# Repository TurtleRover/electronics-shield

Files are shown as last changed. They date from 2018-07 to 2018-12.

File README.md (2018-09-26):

<p align="center">
  <a href="http://turtlerover.com" alt="Turtle Rover">Turtle Rover</a>
</p>
<h1 align="center">Electronics: Shield</h1>
<h4 align="center">This is Raspberry Pi 3 hat designed for Turtle rover.</h4>  

<p align="center">
  <a href="https://github.com/TurtleRover/electronics-shield/releases">
    </a>
  <a href="https://github.com/TurtleRover/electronics-shield/blob/master/LICENSE">
      
  </a>
  <a href="https://twitter.com/TurtleRover">
    
  </a>
</p>
<p align="center">
  <a href="http://turtlerover.com" alt="Website">Website</a> |
  <a href="https://www.facebook.com/TurtleRover/" alt="Facebook">Facebook</a> |
  <a href="https://www.youtube.com/channel/UCxukvEct3wP0S5FACa3uelA" alt="YouTube">YouTube</a>
</p>

## Specification:

Supply voltage: from 12 V to 28 V  
Equipped with TLE9201SG motor controllers  
Continuous output current per channel: 6 A  
Maximum momentary current per channel: 8 A  
Number of channels: 4  
PWM frequency: up to 20 kHz  
3 x adjustable step-down DC-DC 3A converters   
Built-in STM32F030 microprocessor  
Available interfaces:  
- I2C/UART
- SPI
- USB
- SWD
- 3 x servo

Dedicated to Raspberry Pi B + connectors  
Dimensions: 84 x 56 mm

## Board view
PCB board view

## Connectors standard  

| I2C & Servo  | USB & SPI | Programming  |
| --- | --- | --- |
|   |   |  |

## Manufacturing
Manufacture files are generated and added to release.

### Online view of schematics and layout
View this project on [CADLAB.io](https://cadlab.io/project/1250). 

This git project is intended for using with Eagle PCB.

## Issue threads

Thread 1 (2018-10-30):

Add Real Time Clock module

stsdc, 2018-10-30:

Mictronics, 2018-11-11:
Just a tip:
Route the RTC I2C directly to the Raspberry Pi I2C. In addition, route the DS3231 INT/SQW signal to a Raspberry Pi GPIO. The enable both overlays, i2c-rtc and pps-gpio. This way you have the RTC directly supported by kernel.

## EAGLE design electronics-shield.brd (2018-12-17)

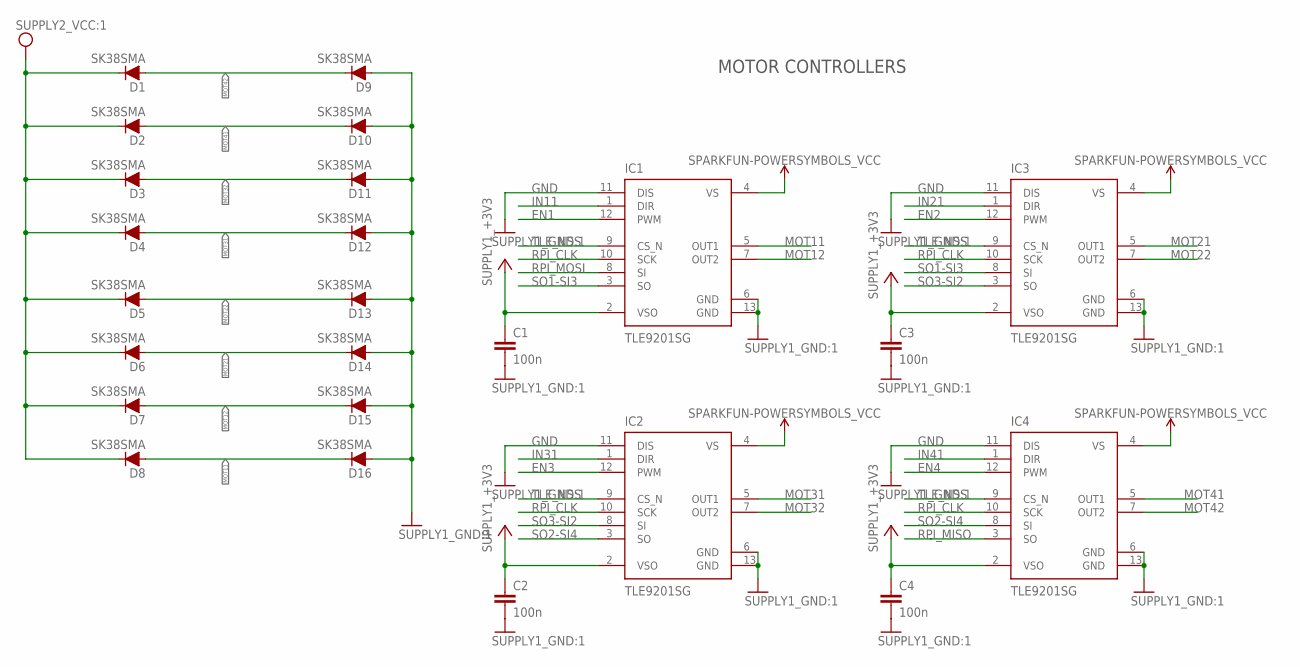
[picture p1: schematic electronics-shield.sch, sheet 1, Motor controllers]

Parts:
C1, C2, C3, C4: 100n; C0603K
D1, D2, D3, D4, D5, D6, D7, D8, D9, D10, D11, D12, D13, D14, D15, D16: SK38SMA; SOD123
IC1, IC2, IC3, IC4: TLE9201SG; PG-DSO-12-9

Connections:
+3V3: C1.1, C2.1, C3.1, C4.1, IC1.2 (VSO), IC2.2 (VSO), IC3.2 (VSO), IC4.2 (VSO); also elsewhere on the board
EN1: IC1.12 (PWM); also elsewhere on the board
EN2: IC3.12 (PWM); also elsewhere on the board
EN3: IC2.12 (PWM); also elsewhere on the board
EN4: IC4.12 (PWM); also elsewhere on the board
GND: C1.2, C2.2, C3.2, C4.2, D9.2 (A), D10.2 (A), D11.2 (A), D12.2 (A), D13.2 (A), D14.2 (A), D15.2 (A), D16.2 (A), IC1.6 (GND), IC1.11 (DIS), IC1.13 (GND), IC2.6 (GND), IC2.11 (DIS), IC2.13 (GND), IC3.6 (GND), IC3.11 (DIS), IC3.13 (GND), IC4.6 (GND), IC4.11 (DIS), IC4.13 (GND); also elsewhere on the board
IN11: IC1.1 (DIR); also elsewhere on the board
IN21: IC3.1 (DIR); also elsewhere on the board
IN31: IC2.1 (DIR); also elsewhere on the board
IN41: IC4.1 (DIR); also elsewhere on the board
MOT11: D8.2 (A), D16.1 (C), IC1.5 (OUT1); also elsewhere on the board
MOT12: D7.2 (A), D15.1 (C), IC1.7 (OUT2); also elsewhere on the board
MOT21: D6.2 (A), D14.1 (C), IC3.5 (OUT1); also elsewhere on the board
MOT22: D5.2 (A), D13.1 (C), IC3.7 (OUT2); also elsewhere on the board
MOT31: D4.2 (A), D12.1 (C), IC2.5 (OUT1); also elsewhere on the board
MOT32: D3.2 (A), D11.1 (C), IC2.7 (OUT2); also elsewhere on the board
MOT41: D2.2 (A), D10.1 (C), IC4.5 (OUT1); also elsewhere on the board
MOT42: D1.2 (A), D9.1 (C), IC4.7 (OUT2); also elsewhere on the board
RPI_CLK: IC1.10 (SCK), IC2.10 (SCK), IC3.10 (SCK), IC4.10 (SCK); also elsewhere on the board
RPI_MISO: IC4.3 (SO); also elsewhere on the board
RPI_MOSI: IC1.8 (SI); also elsewhere on the board
SO1-SI3: IC1.3 (SO), IC3.8 (SI)
SO2-SI4: IC2.3 (SO), IC4.8 (SI)
SO3-SI2: IC2.8 (SI), IC3.3 (SO)
TLE_NSS: IC1.9 (CS_N), IC2.9 (CS_N), IC3.9 (CS_N), IC4.9 (CS_N); also elsewhere on the board
VCC: D1.1 (C), D2.1 (C), D3.1 (C), D4.1 (C), D5.1 (C), D6.1 (C), D7.1 (C), D8.1 (C), IC1.4 (VS), IC2.4 (VS), IC3.4 (VS), IC4.4 (VS); also elsewhere on the board

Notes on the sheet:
MOTOR CONTROLLERS

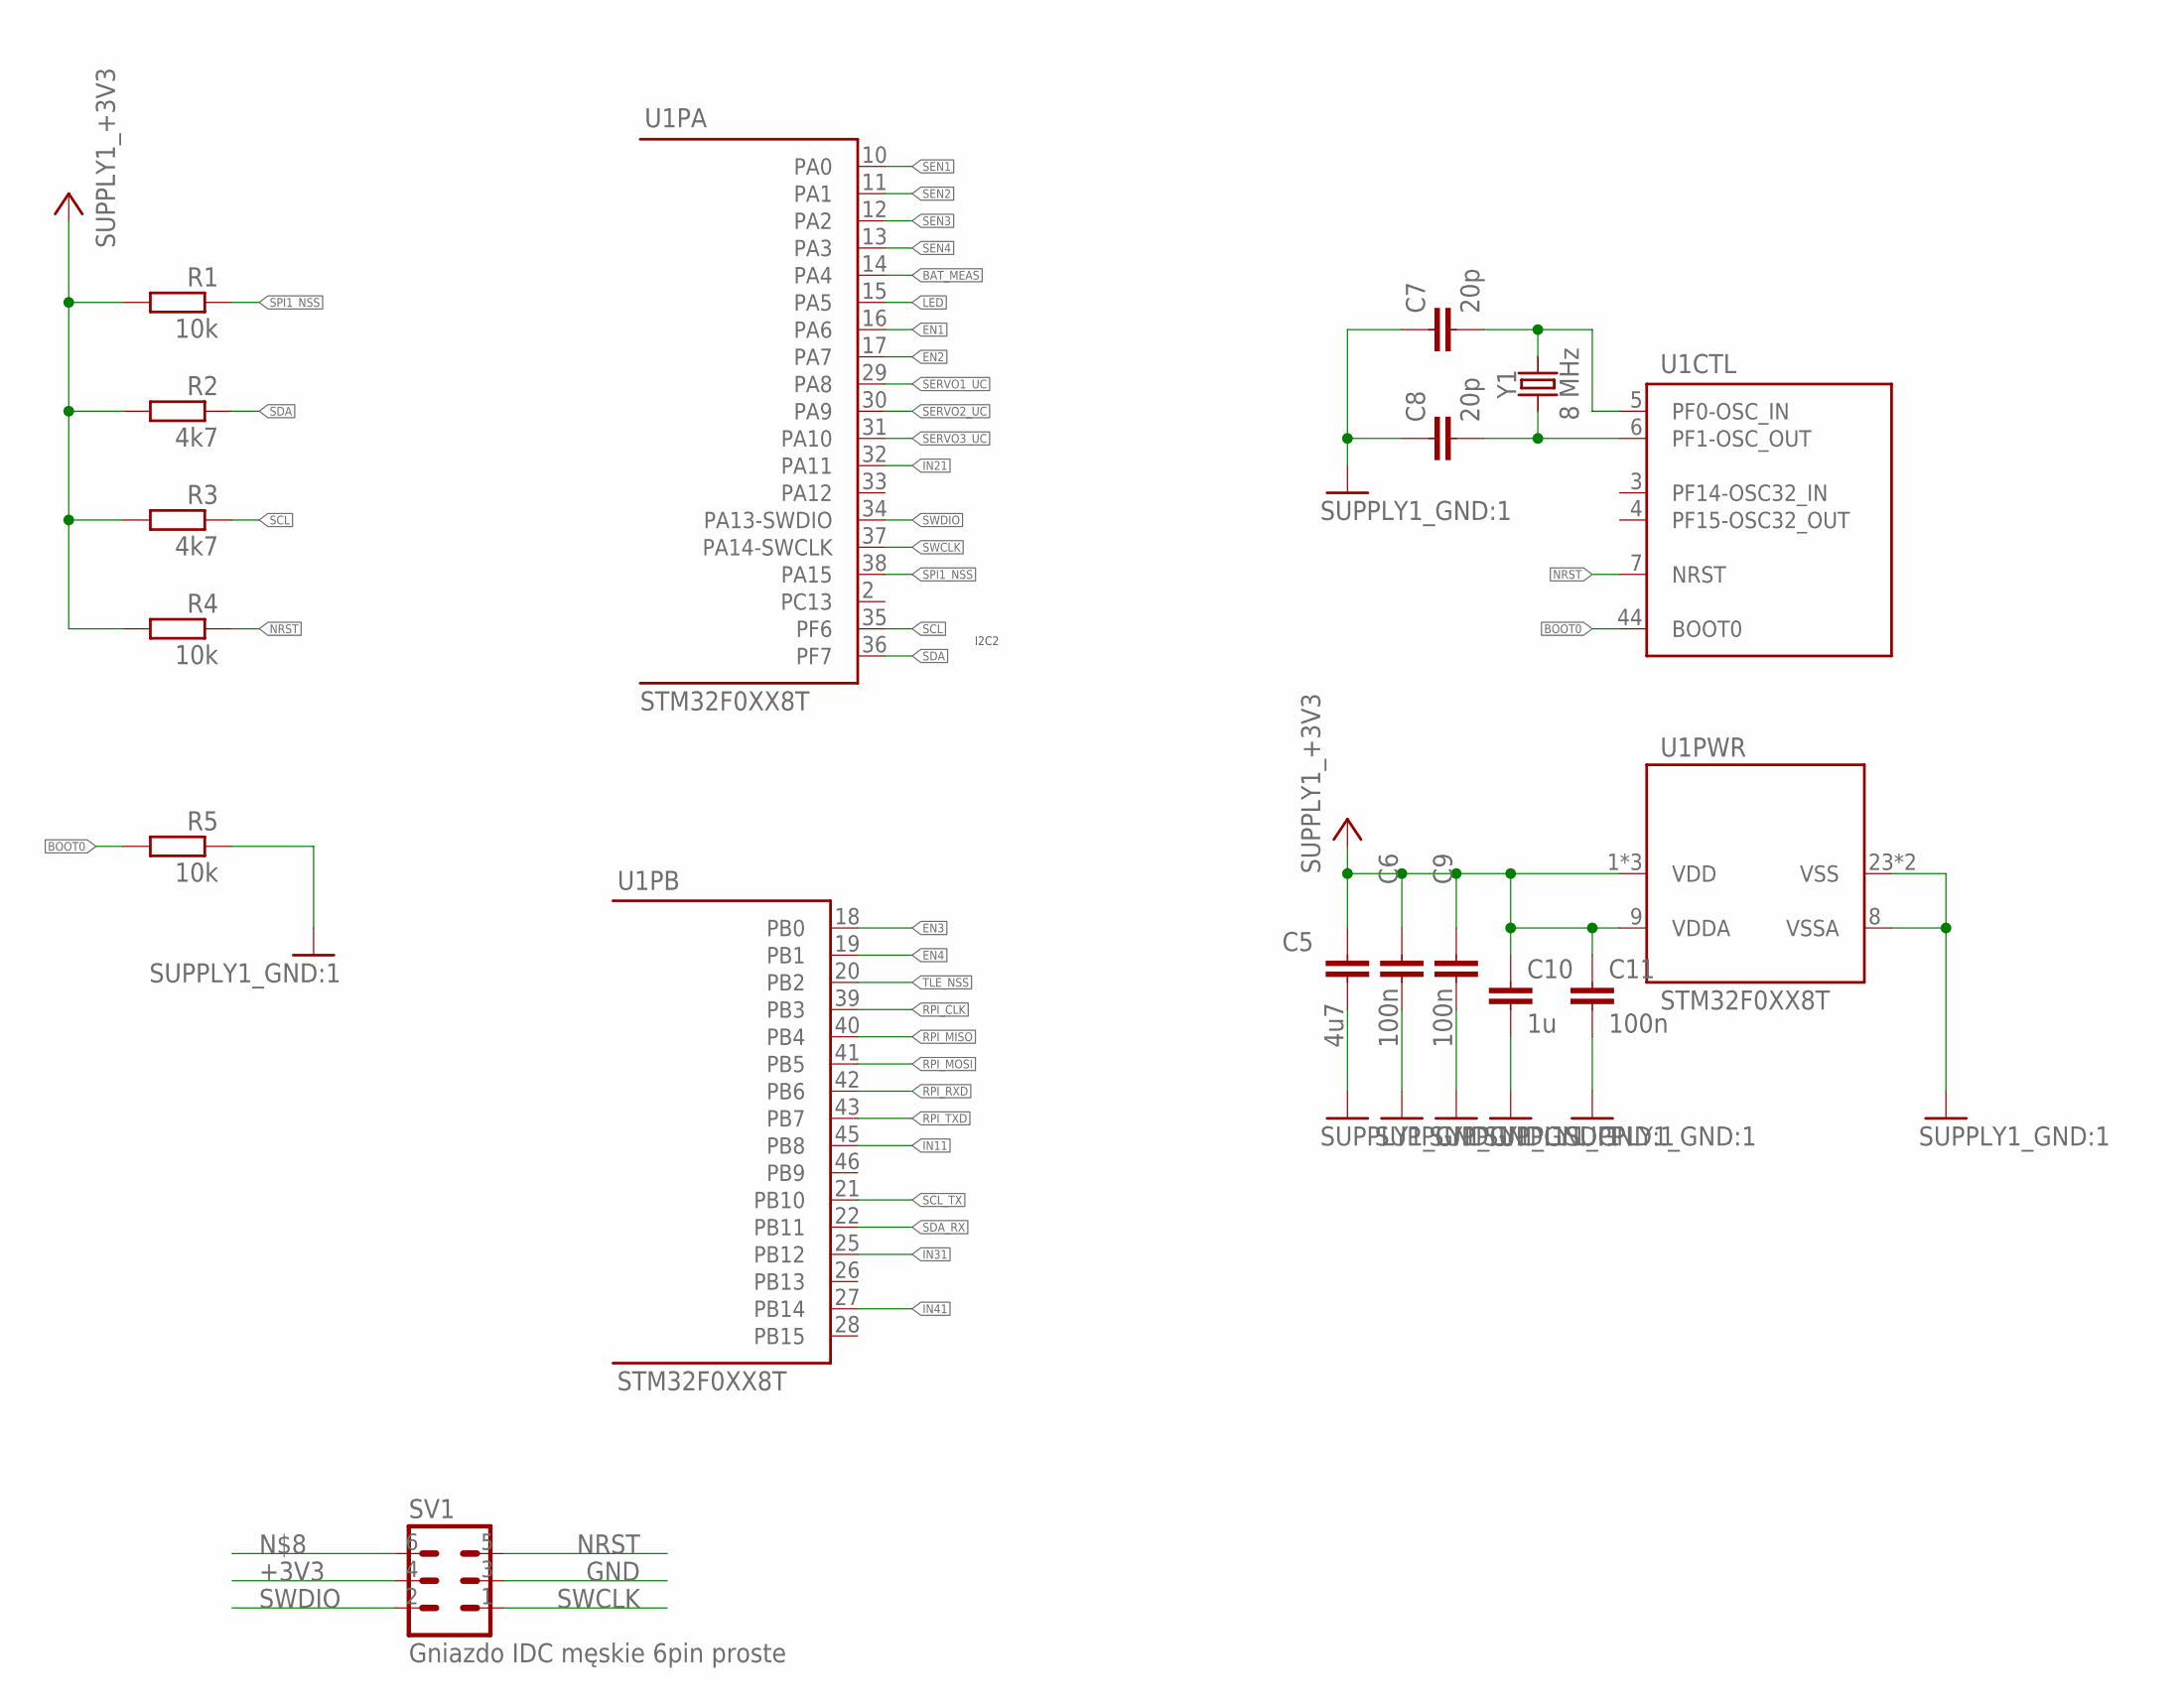
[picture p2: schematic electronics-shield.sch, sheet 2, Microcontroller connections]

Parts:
C5: 4u7; C0603K
C6, C9, C11: 100n; C0603K
C7, C8: 20p; C0603K
C10: 1u; C0603K
R1, R4, R5: 10k; R0603
R2, R3: 4k7; R0603
SV1: Gniazdo IDC męskie 6pin proste; ML6
U1: STM32F0XX8T; LQFP48
Y1: 8 MHz; HC49UP

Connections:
+3V3: C5.1, C6.1, C9.1, C10.1, C11.1, R1.2, R2.2, R3.2, R4.2, SV1.4, U1.1 (VDD), U1.9 (VDDA), U1.24 (VDD), U1.48 (VDD); also elsewhere on the board
BAT_MEAS: U1.14 (PA4); also elsewhere on the board
BOOT0: R5.2, U1.44 (BOOT0)
EN1: U1.16 (PA6); also elsewhere on the board
EN2: U1.17 (PA7); also elsewhere on the board
EN3: U1.18 (PB0); also elsewhere on the board
EN4: U1.19 (PB1); also elsewhere on the board
GND: C5.2, C6.2, C7.1, C8.1, C9.2, C10.2, C11.2, R5.1, SV1.3, U1.8 (VSSA), U1.23 (VSS), U1.47 (VSS); also elsewhere on the board
IN11: U1.45 (PB8); also elsewhere on the board
IN21: U1.32 (PA11); also elsewhere on the board
IN31: U1.25 (PB12); also elsewhere on the board
IN41: U1.27 (PB14); also elsewhere on the board
LED: U1.15 (PA5)
NRST: R4.1, SV1.5, U1.7 (NRST); also elsewhere on the board
OSCILATOR_N: C7.2, U1.5 (PF0-OSC_IN), Y1.2
OSCILATOR_P: C8.2, U1.6 (PF1-OSC_OUT), Y1.1
RPI_CLK: U1.39 (PB3); also elsewhere on the board
RPI_MISO: U1.40 (PB4); also elsewhere on the board
RPI_MOSI: U1.41 (PB5); also elsewhere on the board
RPI_RXD: U1.42 (PB6); also elsewhere on the board
RPI_TXD: U1.43 (PB7); also elsewhere on the board
SCL: R3.1, U1.35 (PF6); also elsewhere on the board
SCL_TX: U1.21 (PB10); also elsewhere on the board
SDA: R2.1, U1.36 (PF7); also elsewhere on the board
SDA_RX: U1.22 (PB11); also elsewhere on the board
SEN1: U1.10 (PA0)
SEN2: U1.11 (PA1)
SEN3: U1.12 (PA2)
SEN4: U1.13 (PA3)
SERVO1_UC: U1.29 (PA8); also elsewhere on the board
SERVO2_UC: U1.30 (PA9); also elsewhere on the board
SERVO3_UC: U1.31 (PA10); also elsewhere on the board
SPI1_NSS: R1.1, U1.38 (PA15); also elsewhere on the board
SWCLK: SV1.1, U1.37 (PA14-SWCLK); also elsewhere on the board
SWDIO: SV1.2, U1.34 (PA13-SWDIO); also elsewhere on the board
TLE_NSS: U1.20 (PB2); also elsewhere on the board

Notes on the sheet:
I2C2

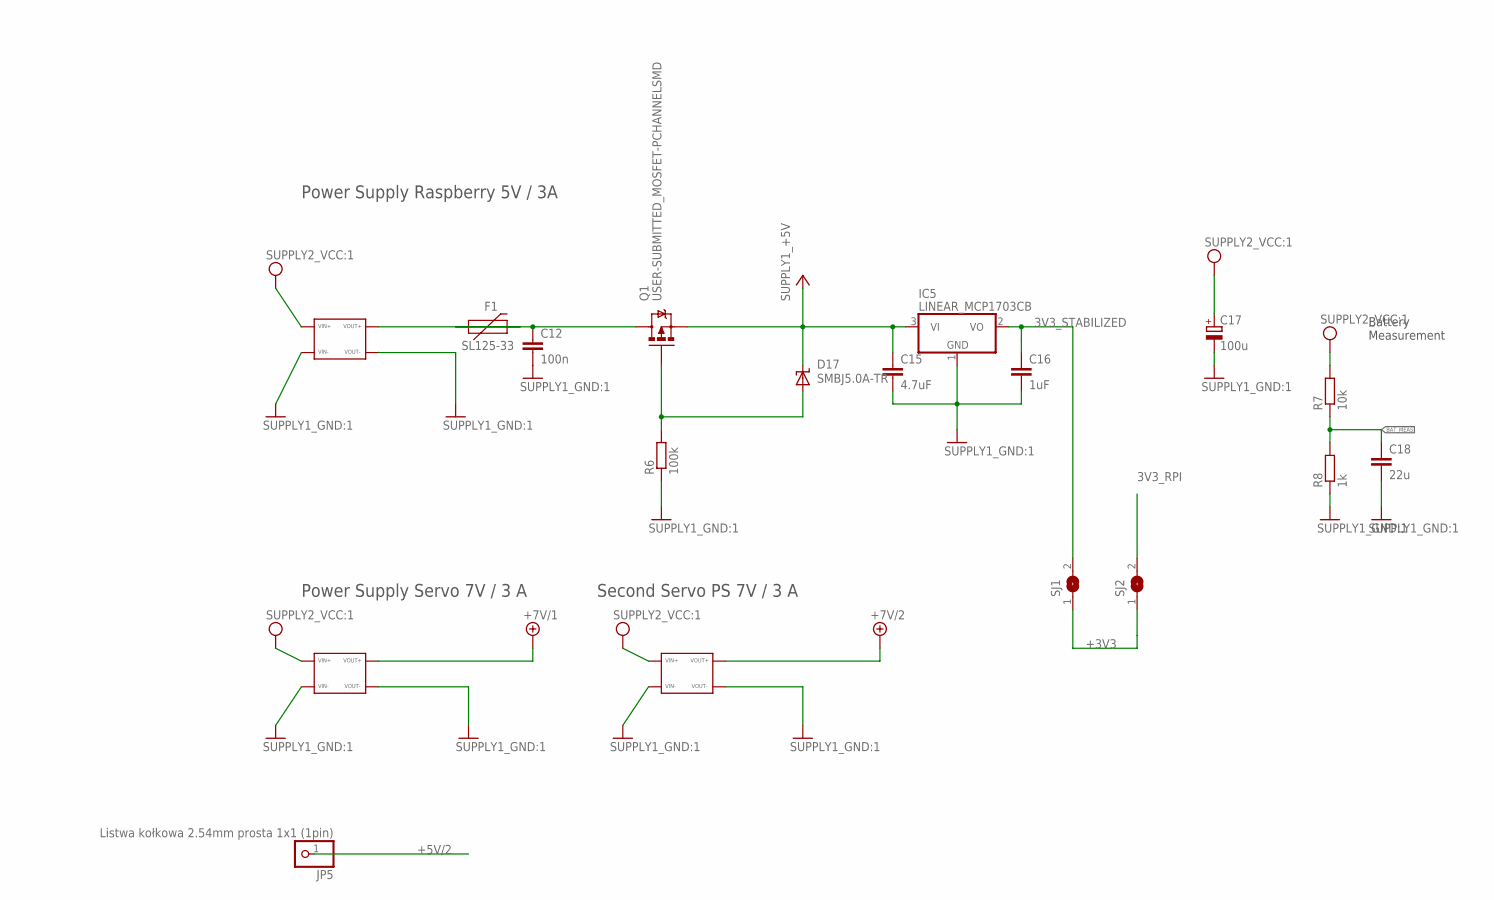
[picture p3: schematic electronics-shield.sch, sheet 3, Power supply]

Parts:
C12: 100n; C0603K
C15: 4.7uF; C0603K
C16: 1uF; C0603K
C17: 100u; FI8_6.2
C18: 22u; C0603K
D17: SMBJ5.0A-TR; SMBJ
F1: SL125-33; FUSC7351X125
IC5: LINEAR_MCP1703CB; LINEAR_SOT23
IC6, IC7, IC8: Moduł przetwornicy DC-DC Step-down 4.5..28V --- r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; DC-BRICK
JP5: Listwa kołkowa 2.54mm prosta 1x1 (1pin); 1X01
Q1: USER-SUBMITTED_MOSFET-PCHANNELSMD; USER-SUBMITTED_SOT23-3
R6: 100k; R0603
R7: 10k; R0603
R8: 1k; R0603
SJ1, SJ2: SOLDER_JUMPER; SJ

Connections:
3V3_RPI: SJ2.2; also elsewhere on the board
3V3_STABILIZED: C16.1, IC5.2 (VO), SJ1.2
5V_NOT_TRIMMED: C12.1, F1.1, Q1.3 (D)
+3V3: SJ1.1, SJ2.1; also elsewhere on the board
+5V: C15.1, D17.C, IC5.3 (VI), Q1.2 (S); also elsewhere on the board
+5V/2: JP5.1; also elsewhere on the board
+5V_RAW: F1.2, IC6.OUT1+1 (VOUT+)
+7V/1: IC7.OUT1+1 (VOUT+); also elsewhere on the board
+7V/2: IC8.OUT1+1 (VOUT+); also elsewhere on the board
BAT_MEAS: C18.1, R7.1, R8.2; also elsewhere on the board
D1-R3: D17.A, Q1.1 (G), R6.2
GND: C12.2, C15.2, C16.2, C17.-, C18.2, IC5.1 (GND), IC6.IN1-1 (VIN-), IC6.OUT1-1 (VOUT-), IC7.IN1-1 (VIN-), IC7.OUT1-1 (VOUT-), IC8.IN1-1 (VIN-), IC8.OUT1-1 (VOUT-), R6.1, R8.1; also elsewhere on the board
VCC: C17.+, IC6.IN1+1 (VIN+), IC7.IN1+1 (VIN+), IC8.IN1+1 (VIN+), R7.2; also elsewhere on the board

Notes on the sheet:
Power Supply Raspberry 5V / 3A
Power Supply Servo 7V / 3 A
Second Servo PS 7V / 3 A
Battery Measurement

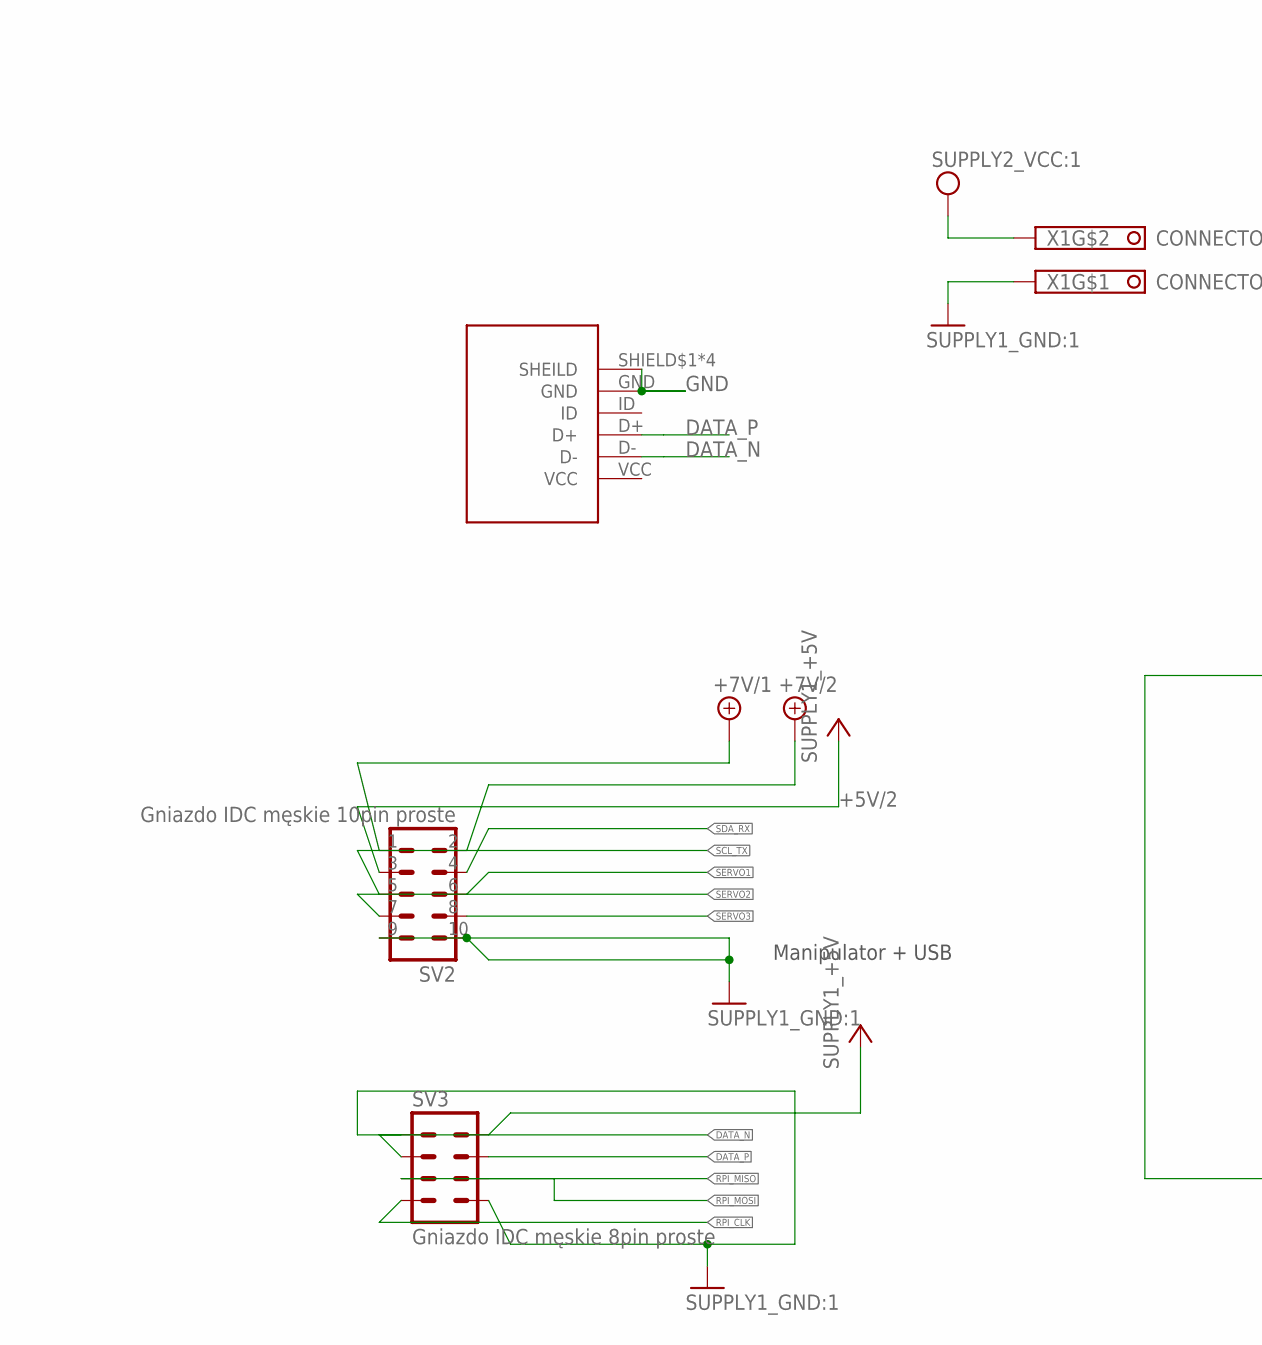
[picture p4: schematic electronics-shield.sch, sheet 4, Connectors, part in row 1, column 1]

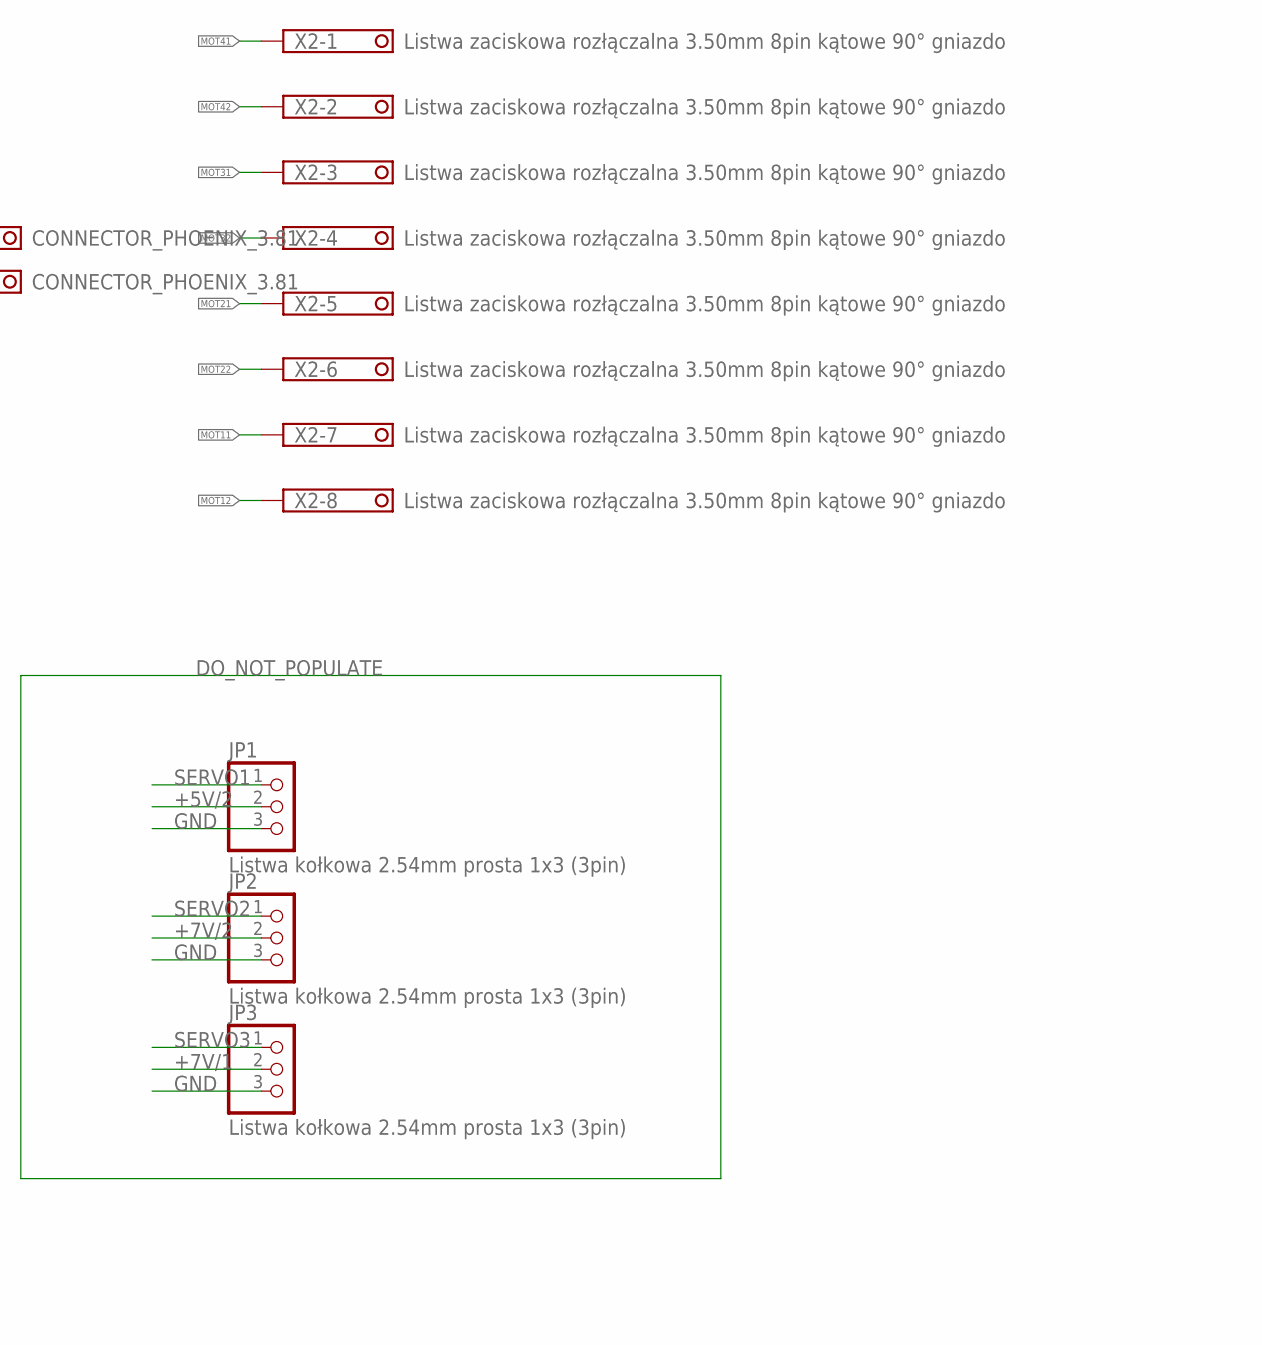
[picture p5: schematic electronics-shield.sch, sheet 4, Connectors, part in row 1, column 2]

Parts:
J1: USB-MICRO-B
JP1, JP2, JP3: Listwa kołkowa 2.54mm prosta 1x3 (3pin); 1X03_ROUND_DNP
SV2: Gniazdo IDC męskie 10pin proste; ML10
SV3: Gniazdo IDC męskie 8pin proste; ML8
X1: CONNECTOR_PHOENIX_3.81; 3.81MM_2PIN
X2: Listwa zaciskowa rozłączalna 3.50mm 8pin kątowe 9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; 3.5MM_8PIN

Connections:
+5V: SV3.2; also elsewhere on the board
+5V/2: JP1.2, SV2.3; also elsewhere on the board
+7V/1: JP3.2, SV2.1; also elsewhere on the board
+7V/2: JP2.2, SV2.2; also elsewhere on the board
DATA_N: J1.D-, SV3.3
DATA_P: J1.D+, SV3.4
GND: J1.GND, J1.SHIELD$1 (SHEILD), J1.SHIELD$2 (SHEILD), J1.SHIELD$3 (SHEILD), J1.SHIELD$4 (SHEILD), JP1.3, JP2.3, JP3.3, SV2.9, SV2.10, SV3.1, SV3.8, X1.1; also elsewhere on the board
MOT11: X2.7; also elsewhere on the board
MOT12: X2.8; also elsewhere on the board
MOT21: X2.5; also elsewhere on the board
MOT22: X2.6; also elsewhere on the board
MOT31: X2.3; also elsewhere on the board
MOT32: X2.4; also elsewhere on the board
MOT41: X2.1; also elsewhere on the board
MOT42: X2.2; also elsewhere on the board
RPI_CLK: SV3.7; also elsewhere on the board
RPI_MISO: SV3.5; also elsewhere on the board
RPI_MOSI: SV3.6; also elsewhere on the board
SCL_TX: SV2.5; also elsewhere on the board
SDA_RX: SV2.4; also elsewhere on the board
SERVO1: JP1.1, SV2.6; also elsewhere on the board
SERVO2: JP2.1, SV2.7; also elsewhere on the board
SERVO3: JP3.1, SV2.8; also elsewhere on the board
VCC: X1.2; also elsewhere on the board

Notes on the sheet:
Manipulator + USB

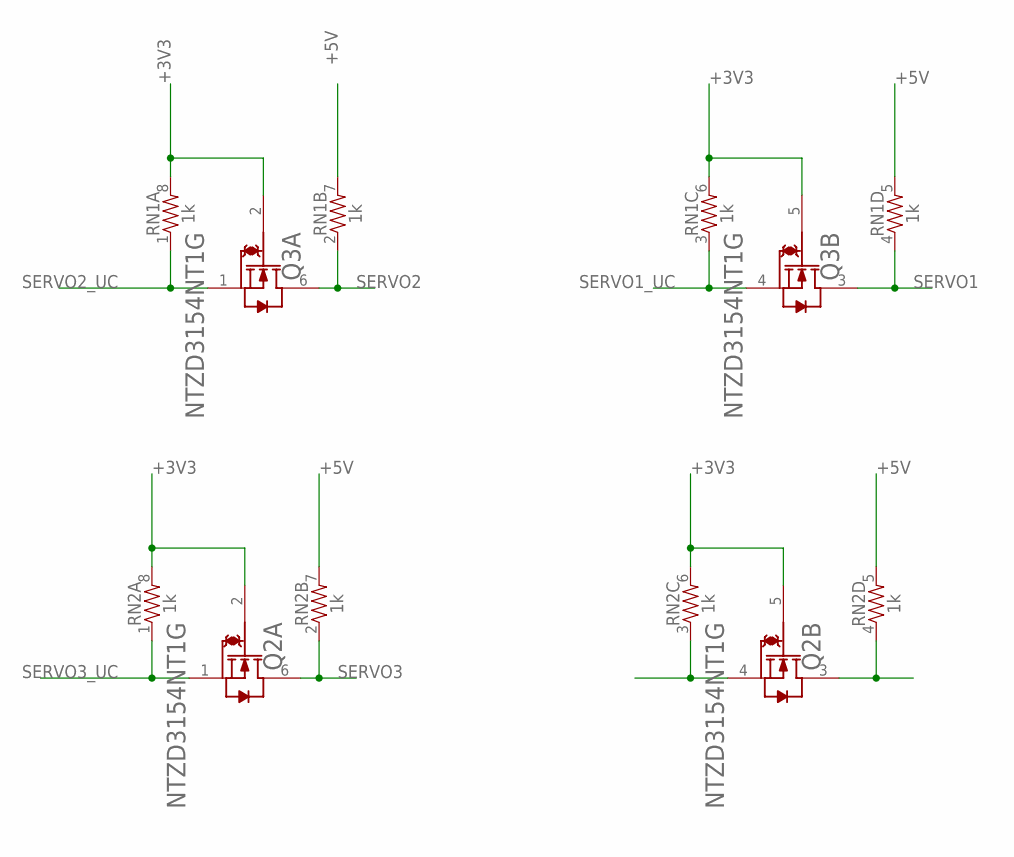
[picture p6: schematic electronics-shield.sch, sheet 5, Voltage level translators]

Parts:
Q2, Q3: NTZD3154NT1G; ON-SEMICONDUCTOR---NTZD3154NT1G_ON_SEMICONDUCTOR_NTZD3154NT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
RN1, RN2: 1k; 0805-ARV

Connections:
+3V3: Q2.2 (G1), Q2.5 (G2), Q3.2 (G1), Q3.5 (G2), RN1.6 (2), RN1.8 (2), RN2.6 (2), RN2.8 (2); also elsewhere on the board
+5V: RN1.5 (2), RN1.7 (2), RN2.5 (2), RN2.7 (2); also elsewhere on the board
unnamed: Q2.4 (S2), RN2.3 (1)
unnamed: Q2.3 (D2), RN2.4 (1)
SERVO1: Q3.3 (D2), RN1.4 (1); also elsewhere on the board
SERVO1_UC: Q3.4 (S2), RN1.3 (1); also elsewhere on the board
SERVO2: Q3.6 (D1), RN1.2 (1); also elsewhere on the board
SERVO2_UC: Q3.1 (S1), RN1.1; also elsewhere on the board
SERVO3: Q2.6 (D1), RN2.2 (1); also elsewhere on the board
SERVO3_UC: Q2.1 (S1), RN2.1; also elsewhere on the board

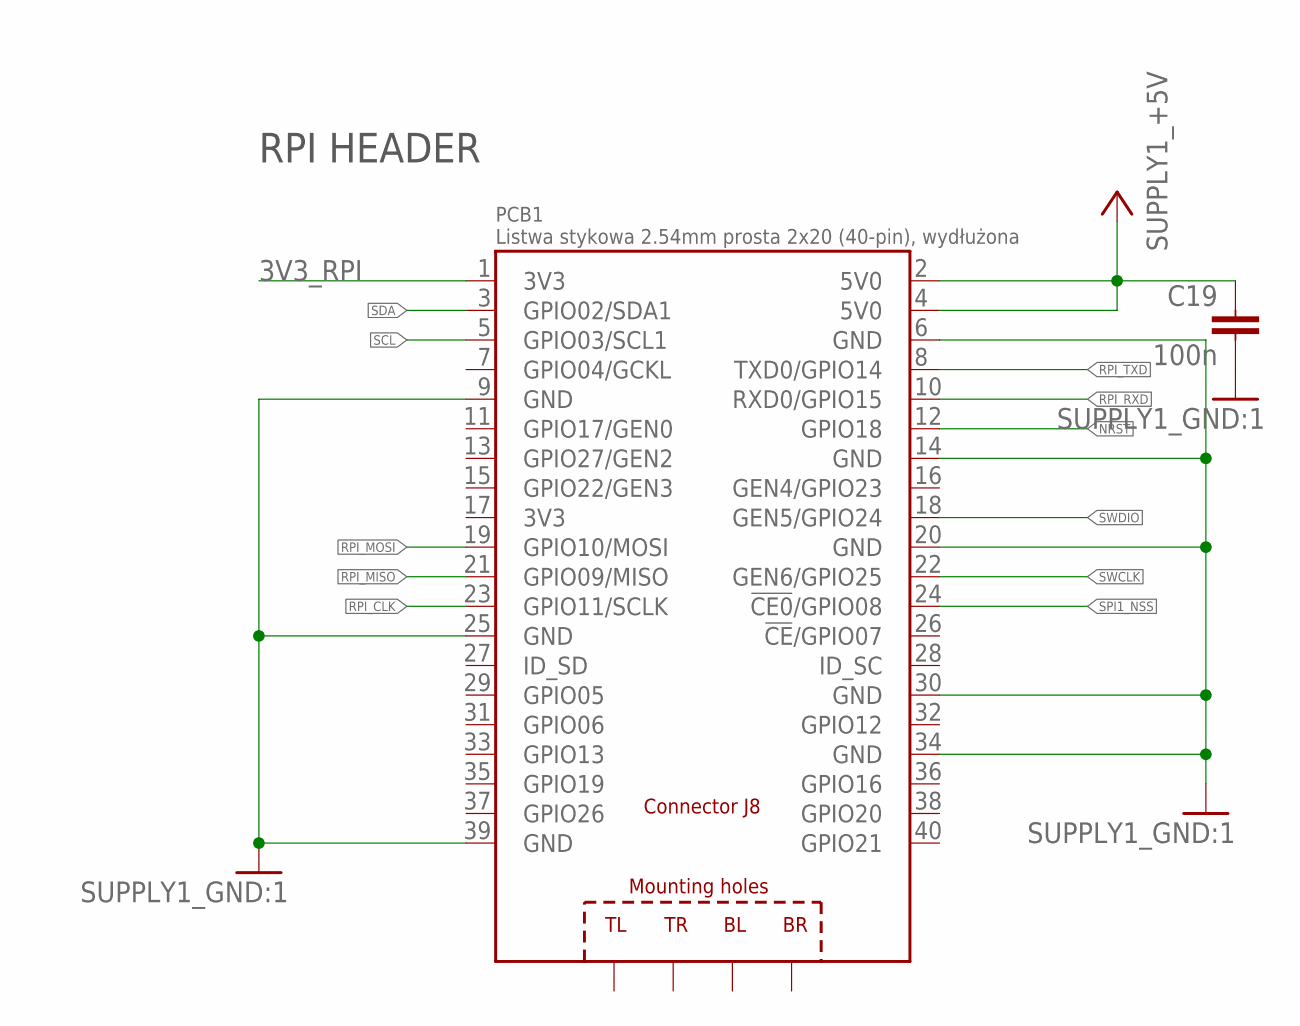
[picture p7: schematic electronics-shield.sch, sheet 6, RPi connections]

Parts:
C19: 100n; C0603K
PCB1: Listwa stykowa 2.54mm prosta 2x20 (40-pin), wydłu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; RASPBERRY_PI_B+_CONNECTOR

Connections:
3V3: PCB1.17 (3V3)
3V3_RPI: PCB1.1 (3V3); also elsewhere on the board
+5V: C19.1, PCB1.2 (5V0), PCB1.4 (5V0); also elsewhere on the board
GND: C19.2, PCB1.6 (GND), PCB1.9 (GND), PCB1.14 (GND), PCB1.20 (GND), PCB1.25 (GND), PCB1.30 (GND), PCB1.34 (GND), PCB1.39 (GND); also elsewhere on the board
NRST: PCB1.12 (GPIO18); also elsewhere on the board
RPI_CLK: PCB1.23 (GPIO11/SCLK); also elsewhere on the board
RPI_MISO: PCB1.21 (GPIO09/MISO); also elsewhere on the board
RPI_MOSI: PCB1.19 (GPIO10/MOSI); also elsewhere on the board
RPI_RXD: PCB1.10 (RXD0/GPIO15); also elsewhere on the board
RPI_TXD: PCB1.8 (TXD0/GPIO14); also elsewhere on the board
SCL: PCB1.5 (GPIO03/SCL1); also elsewhere on the board
SDA: PCB1.3 (GPIO02/SDA1); also elsewhere on the board
SPI1_NSS: PCB1.24 (!CE0!/GPIO08); also elsewhere on the board
SWCLK: PCB1.22 (GEN6/GPIO25); also elsewhere on the board
SWDIO: PCB1.18 (GEN5/GPIO24); also elsewhere on the board

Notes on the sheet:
RPI HEADER

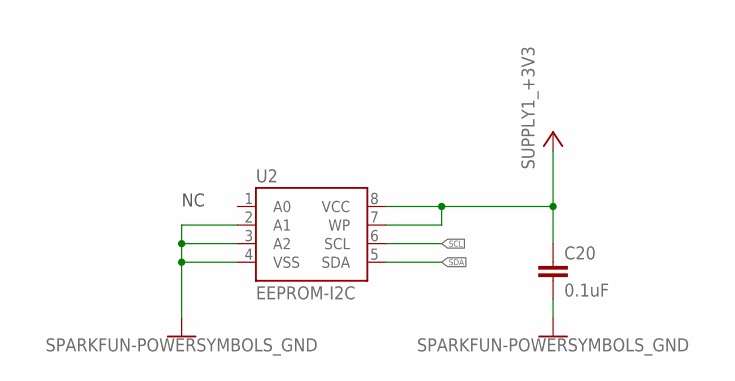
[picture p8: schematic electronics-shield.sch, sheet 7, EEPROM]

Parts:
C20: 0.1uF; C0603K
U2: EEPROM-I2C; SO-08

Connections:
+3V3: C20.1, U2.7 (WP), U2.8 (VCC); also elsewhere on the board
GND: C20.2, U2.2 (A1), U2.3 (A2), U2.4 (VSS); also elsewhere on the board
SCL: U2.6 (SCL); also elsewhere on the board
SDA: U2.5 (SDA); also elsewhere on the board

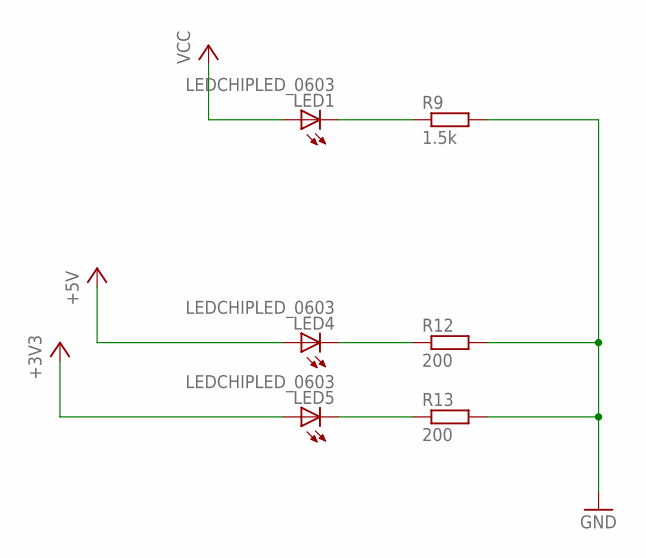
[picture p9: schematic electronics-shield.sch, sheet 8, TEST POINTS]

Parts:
LED1, LED4, LED5: LEDCHIPLED_0603; CHIPLED_0603
R9: 1.5k; R0603
R12, R13: 200; R0603

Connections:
+3V3: LED5.A; also elsewhere on the board
+5V: LED4.A; also elsewhere on the board
GND: R9.2, R12.2, R13.2; also elsewhere on the board
unnamed: LED1.C, R9.1
unnamed: LED4.C, R12.1
unnamed: LED5.C, R13.1
VCC: LED1.A; also elsewhere on the board

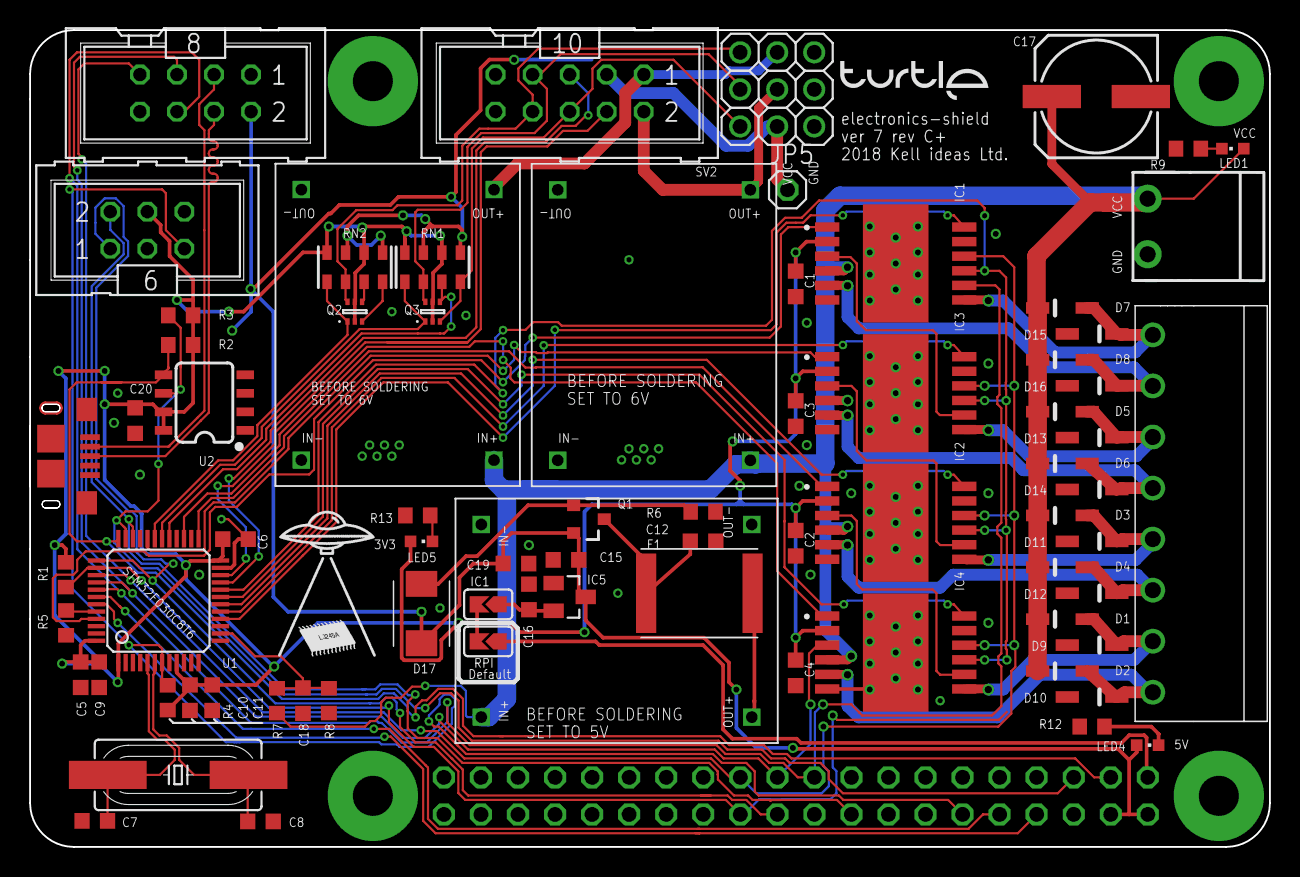
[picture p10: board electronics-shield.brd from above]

Board: 2 copper layers, 85.0 x 56.0 mm, 79 parts (0 on the bottom side), 62 nets.

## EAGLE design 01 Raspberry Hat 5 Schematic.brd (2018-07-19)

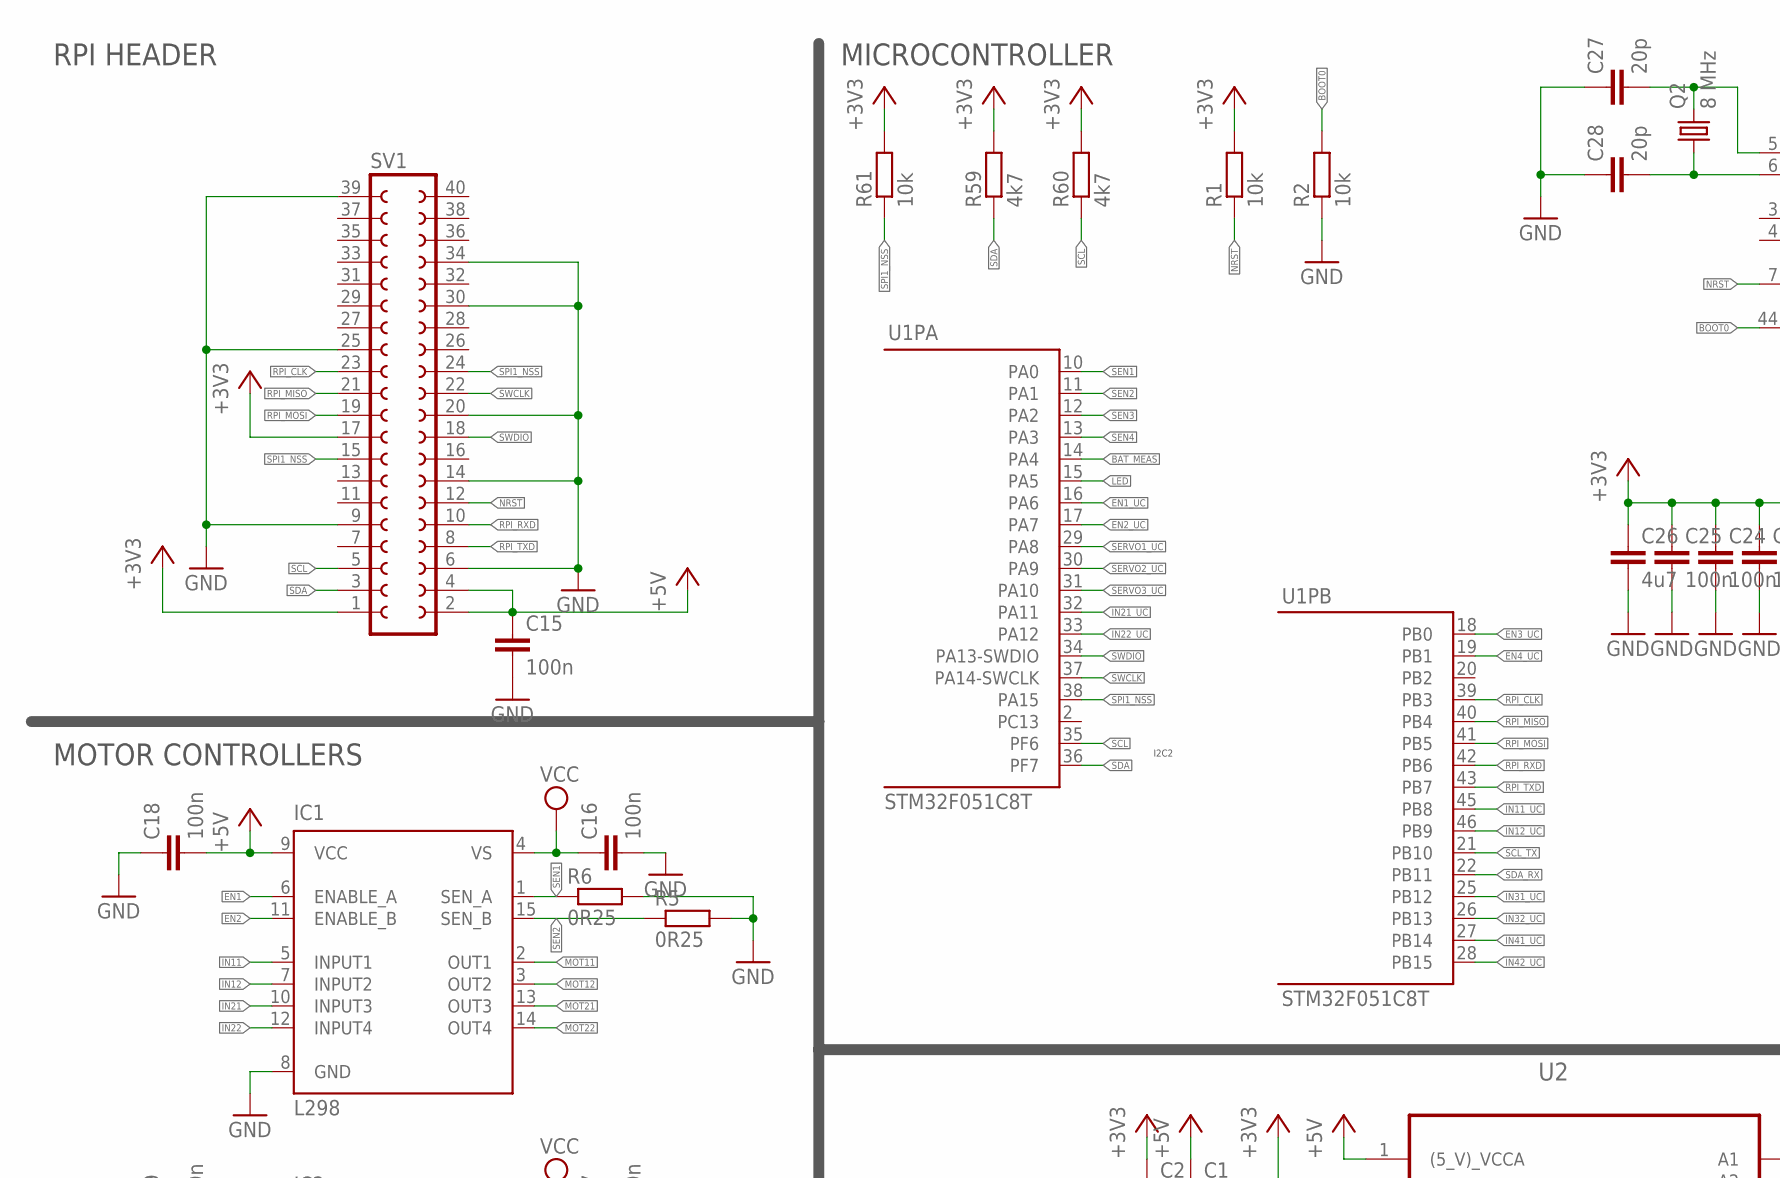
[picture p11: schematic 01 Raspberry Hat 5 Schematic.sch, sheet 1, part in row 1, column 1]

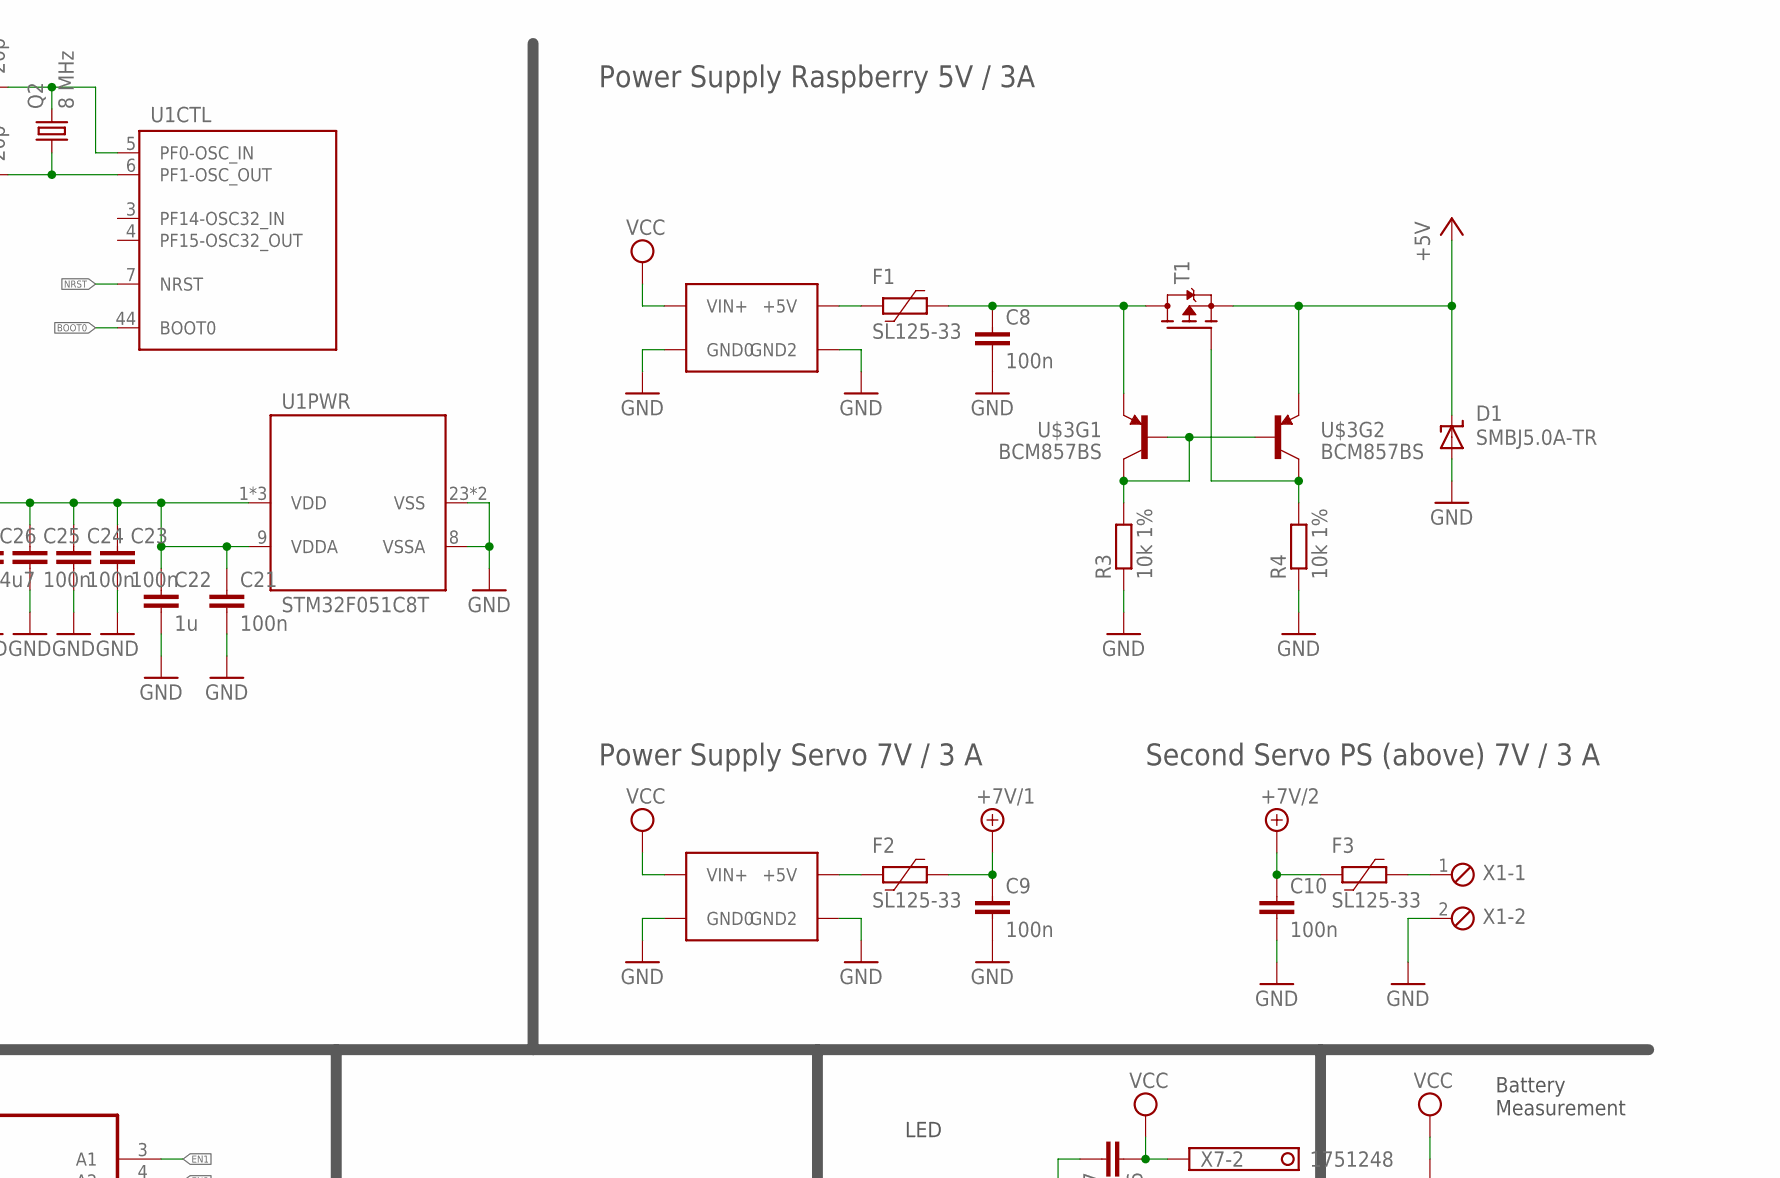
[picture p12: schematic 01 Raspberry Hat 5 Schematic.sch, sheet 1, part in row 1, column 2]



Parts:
C1, C2, C3, C4, C8, C9, C10, C11, C12, C13, C14, C15, C16, C17, C18, C19, C21, C23, C24, C25: 100n; C0805
C5: 100u; 153CLV-0807
C6, C26: 4u7; C0805
C20: 47u; C0805
C22: 1u; C0805
C27, C28: 20p; C0805
D1: SMBJ5.0A-TR; SMBJ
D2, D3, D4, D5, D6, D7, D8, D9, D10, D11, D12, D13, D14, D15, D16, D17: SK38SMA; DO214AC
F1, F2, F3: SL125-33; 2920L
IC1, IC2: L298; MULTIWATT-15
Q2: 8 MHz; HC49UP
R1, R2, R45, R61, R62, R63: 10k; M0805
R3, R4: 10k 1%; M0805
R5, R6, R7, R8: 0R25; R2512
R46: 2k2; M0805
R48: 100k; M0805
R49: 100; M0805
R59, R60: 4k7; M0805
SV1: FE20-2
T1: MOSFET-P-SOT23; SOT23
T14: BSS306N; SOT23
U1: STM32F051C8T; LQFP48
U2, U3: SN74LVC4245APWR; SOP65P640X120-24N
U$2, U$4: LM2596_CONVERTER
U$3: BCM857BS; SOT363
X1: MPT2; 2POL254
X2: 2508-; PAK100/2500-10
X3: MC2
X4: 2510-; PAK100/2500-10
X6: 1751303
X7: 1751248

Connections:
+3V3: C2.1, C4.1, C21.1, C22.1, C23.1, C24.1, C25.1, C26.1, R1.2, R59.2, R60.2, R61.2, SV1.1, SV1.17, U1.1 (VDD), U1.9 (VDDA), U1.24 (VDD), U1.48 (VDD), U2.23 (VCCB_(3.3_V)), U2.24 (VCCB_(3.3_V)_2), U3.23 (VCCB_(3.3_V)), U3.24 (VCCB_(3.3_V)_2)
+7V/1: C9.1, F2.1, X4.1
+7V/2: C10.1, F3.2, X4.2
BAT_MEAS: C20.1, R45.1, R46.2, U1.14 (PA4)
BOOT0: R2.2, U1.44 (BOOT0)
DATA+: X2.4; also elsewhere on the board
DATA-: X2.3; also elsewhere on the board
EN1: IC1.6 (ENABLE_A), U2.3 (A1)
EN1_UC: U1.16 (PA6), U2.21 (B1)
EN2: IC1.11 (ENABLE_B), U2.4 (A2)
EN2_UC: U1.17 (PA7), U2.20 (B2)
EN3: IC2.6 (ENABLE_A), U2.5 (A3)
EN3_UC: U1.18 (PB0), U2.19 (B3)
EN4: IC2.11 (ENABLE_B), U2.6 (A4)
EN4_UC: U1.19 (PB1), U2.18 (B4)
GND: C1.2, C2.2, C3.2, C4.2, C5.-, C6.2, C8.2, C9.2, C10.2, C11.2, C12.2, C13.2, C14.2, C15.2, C16.2, C17.2, C18.1, C19.1, C20.2, C21.2, C22.2, C23.2, C24.2, C25.2, C26.2, C27.1, C28.1, D1.A, D6.A, D7.A, D8.A, D9.A, D14.A, D15.A, D16.A, D17.A, IC1.8 (GND), IC2.8 (GND), R2.1, R3.1, R4.1, R5.2, R6.2, R7.2, R8.2, R46.1, R48.1, R62.2, R63.2, SV1.6, SV1.9, SV1.14, SV1.20, SV1.25, SV1.30, SV1.34, SV1.39, T14.2 (S), U1.8 (VSSA), U1.23 (VSS), U1.47 (VSS), U2.11 (GND_3), U2.12 (GND), U2.13 (GND_2), U3.11 (GND_3), U3.12 (GND), U3.13 (GND_2), U$2.GND (GND0), U$2.GND1 (GND2), U$4.GND (GND0), U$4.GND1 (GND2), X1.2, X2.8, X3.1, X4.9, X4.10
IN11: IC1.5 (INPUT1), U2.7 (A5)
IN11_UC: U1.45 (PB8), U2.17 (B5)
IN12: IC1.7 (INPUT2), U2.8 (A6)
IN12_UC: U1.46 (PB9), U2.16 (B6)
IN21: IC1.10 (INPUT3), U2.9 (A7)
IN21_UC: U1.32 (PA11), U2.15 (B7)
IN22: IC1.12 (INPUT4), U2.10 (A8)
IN22_UC: U1.33 (PA12), U2.14 (B8)
IN31: IC2.5 (INPUT1), U3.3 (A1)
IN31_UC: U1.25 (PB12), U3.21 (B1)
IN32: IC2.7 (INPUT2), U3.4 (A2)
IN32_UC: U1.26 (PB13), U3.20 (B2)
IN41: IC2.10 (INPUT3), U3.5 (A3)
IN41_UC: U1.27 (PB14), U3.19 (B3)
IN42: IC2.12 (INPUT4), U3.6 (A4)
IN42_UC: U1.28 (PB15), U3.18 (B4)
LED: R49.2, U1.15 (PA5)
MOT11: D2.A, D6.C, IC1.2 (OUT1), X6.7
MOT12: D3.A, D7.C, IC1.3 (OUT2), X6.8
MOT21: D4.A, D8.C, IC1.13 (OUT3), X6.5
MOT22: D5.A, D9.C, IC1.14 (OUT4), X6.6
MOT31: D10.A, D14.C, IC2.2 (OUT1), X6.3
MOT32: D11.A, D15.C, IC2.3 (OUT2), X6.4
MOT41: D12.A, D16.C, IC2.13 (OUT3), X6.1
MOT42: D13.A, D17.C, IC2.14 (OUT4), X6.2
unnamed: R62.1, U2.2 (DIR), U2.22 (~OE)
unnamed: R63.1, U3.2 (DIR), U3.22 (~OE)
unnamed: F1.2, U$2.+5V
unnamed: C8.1, F1.1, T1.3 (D), U$3.1 (E)
unnamed: F3.1, X1.1
unnamed: R4.2, T1.1 (G), U$3.3 (C)
unnamed: R3.2, U$3.2 (B), U$3.5 (B), U$3.6 (C)
unnamed: F2.2, U$4.+5V
unnamed: R48.2, R49.1, T14.1 (G)
unnamed: T14.3 (D), X7.1
unnamed: C28.2, Q2.1, U1.6 (PF1-OSC_OUT)
unnamed: C27.2, Q2.2, U1.5 (PF0-OSC_IN)
NRST: R1.1, SV1.12, U1.7 (NRST)
RPI_CLK: SV1.23, U1.39 (PB3), X2.7
RPI_MISO: SV1.21, U1.40 (PB4), X2.5
RPI_MOSI: SV1.19, U1.41 (PB5), X2.6
RPI_RXD: SV1.10, U1.42 (PB6)
RPI_TXD: SV1.8, U1.43 (PB7)
SCL: R60.1, SV1.5, U1.35 (PF6)
SCL_TX: U1.21 (PB10), X4.5
SDA: R59.1, SV1.3, U1.36 (PF7)
SEN1: C11.1, IC1.1 (SEN_A), R6.1, U1.10 (PA0)
SEN2: C12.1, IC1.15 (SEN_B), R5.1, U1.11 (PA1)
SEN3: C13.1, IC2.1 (SEN_A), R7.1, U1.12 (PA2)
SEN4: C14.1, IC2.15 (SEN_B), R8.1, U1.13 (PA3)
SERVO1: U3.7 (A5), X4.6
SERVO1_UC: U1.29 (PA8), U3.17 (B5)
SERVO2: U3.8 (A6), X4.7
SERVO2_UC: U1.30 (PA9), U3.16 (B6)
SERVO3: U3.9 (A7), X4.8
SERVO3_UC: U1.31 (PA10), U3.15 (B7)
SPI1_NSS: R61.1, SV1.15, SV1.24, U1.38 (PA15)
SWCLK: SV1.22, U1.37 (PA14-SWCLK)
SWDIO: SV1.18, U1.34 (PA13-SWDIO)
VCC: C5.+, C6.1, C16.1, C17.1, D2.C, D3.C, D4.C, D5.C, D10.C, D11.C, D12.C, D13.C, IC1.4 (VS), IC2.4 (VS), R45.2, U$2.IN+ (VIN+), U$4.IN+ (VIN+), X2.1, X3.2, X7.2

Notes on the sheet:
RPI HEADER
Power Supply Raspberry 5V / 3A
Power Supply Servo 7V / 3 A
Second Servo PS (above) 7V / 3 A
MOTOR CONTROLLERS
MICROCONTROLLER
Battery Measurement
Power Supply and Button
LED
I2C2
B to A
Manipulator + USB

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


Board: 2 copper layers, 100.0 x 68.0 mm, 83 parts (63 on the bottom side), 78 nets.

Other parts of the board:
X5: 2POL254

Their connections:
DATA+: X5.2; also elsewhere on the board
DATA-: X5.1; also elsewhere on the board

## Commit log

2018-07-19 Upload version 5.0.0
    [01 Raspberry Hat 4 Schematic.brd, 01 Raspberry Hat 5 Schematic.brd, 01 Raspberry Hat 5 Schematic.sch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]
2018-07-19 Upload version 6.0.0
    [01 Raspberry Hat 6 Schematic.brd, 01 Raspberry Hat 6 Schematic.sch]
2018-07-19 Upload version 7.0.0
    [01 Raspberry Hat 6 Schematic.brd, 01 Raspberry Hat 6 Schematic.sch, 01 Raspberry Hat 7 Schematic.brd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]
2018-08-02 H-Bridge change from L298P to TLE9201S, better wiring
    [01 Raspberry Hat 7 Schematic.brd, electronics-shield.brd, electronics-shield.sch]
2018-08-11 Changed USB connector from two holes to micro-usb connector, change in voltage translation
    [electronics-shield.brd, electronics-shield.sch]
2018-08-14 Thermal vias and led for checking voltages added
    [electronics-shield.brd, electronics-shield.sch]
2018-08-16 change few footprints, complete wiring
    [electronics-shield.brd, electronics-shield.sch]
2018-09-26 Added place to solder additional DC/DC converter, removed PTC from serwo power lines
    [electronics-shield.brd, electronics-shield.sch]
2018-12-17 7C+ release
    [electronics-shield.brd, electronics-shield.sch]

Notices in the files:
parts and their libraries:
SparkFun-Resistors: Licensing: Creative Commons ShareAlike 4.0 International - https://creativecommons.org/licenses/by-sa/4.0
